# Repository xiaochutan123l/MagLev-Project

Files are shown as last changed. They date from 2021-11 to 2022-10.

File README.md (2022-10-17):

MagLev-Project

[中文版Chinese](https://github.com/xiaochutan123l/MagLev-Project/blob/main/docs/%E4%B8%8A%E6%8B%89%E5%BC%8F%E7%A3%81%E6%82%AC%E6%B5%AE.md)

Pull-up magnetic levitation based on Arduino board.

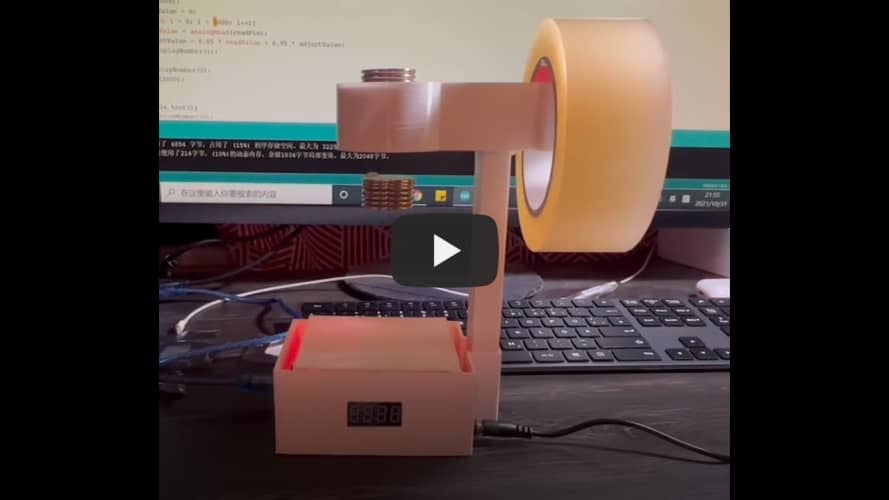
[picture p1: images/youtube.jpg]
(https://youtu.be/WY3Qidg5Ipc)

## Introduction

MagLev-Project is a magnetic levitation project like its name.  Magnet levitation with Arduino or some other MCU is actually an old stuff. There are many tutorial and demonstration on the internet. Here i will share my code and the experience of making it. It may help someone who also wants to make a magnetic levitation device. 

There two types of magnet levitation principle: `Pull-up` and `Push-down`. This project is the other type `Pull-up`. This project includes two versions, `basic version` (manual set parameters for each floater) and `weight adaptive` version.

## Principle

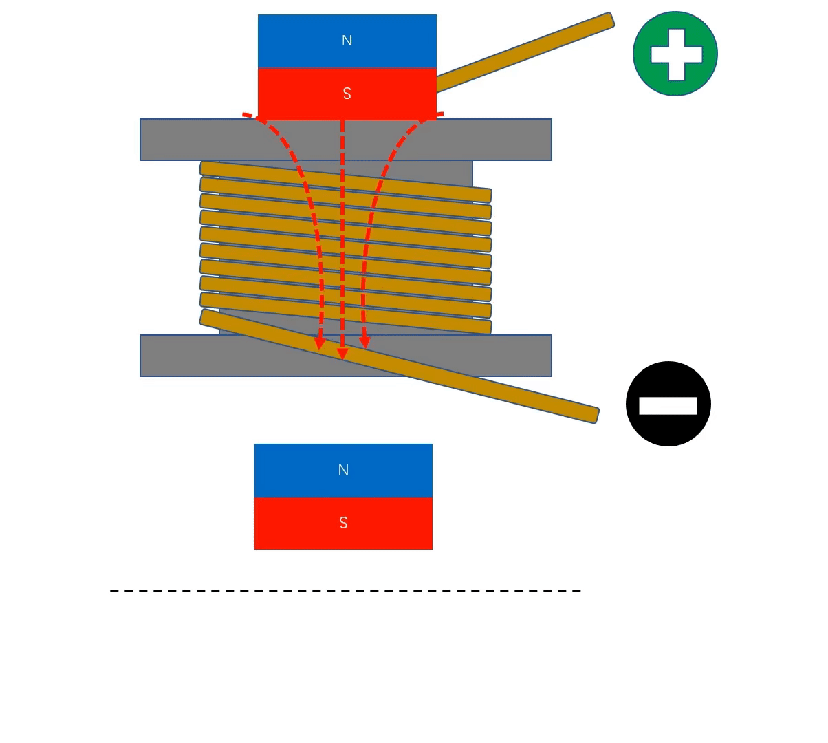
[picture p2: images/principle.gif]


The principle of the levitation is illustrated as in the Gif. The above magnet provides a pull force which can counteract the gravity of the bottom magnet(floater), this critical position is the `AdjustValue` which we want the floater to float. With the help of the above magnet, the electromagnet(copper coil) needs relatively small force to keep the floater at the critical position. 

We can see in this Gif, the levitation process is dynamic. If the floater goes down or up, we can control the coil to produce a pull or push force, by changing the electrodes. The Hall-effect sensor is very sensitive, thus a slight movement of the floater will be detected, and a corresponding controlling for the coil will then be taken. The floater can float stably at a fixed position.

## Hardware components

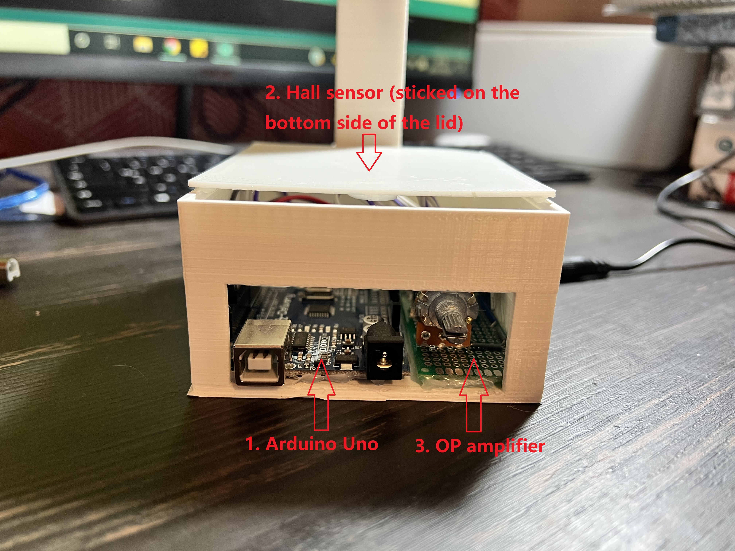
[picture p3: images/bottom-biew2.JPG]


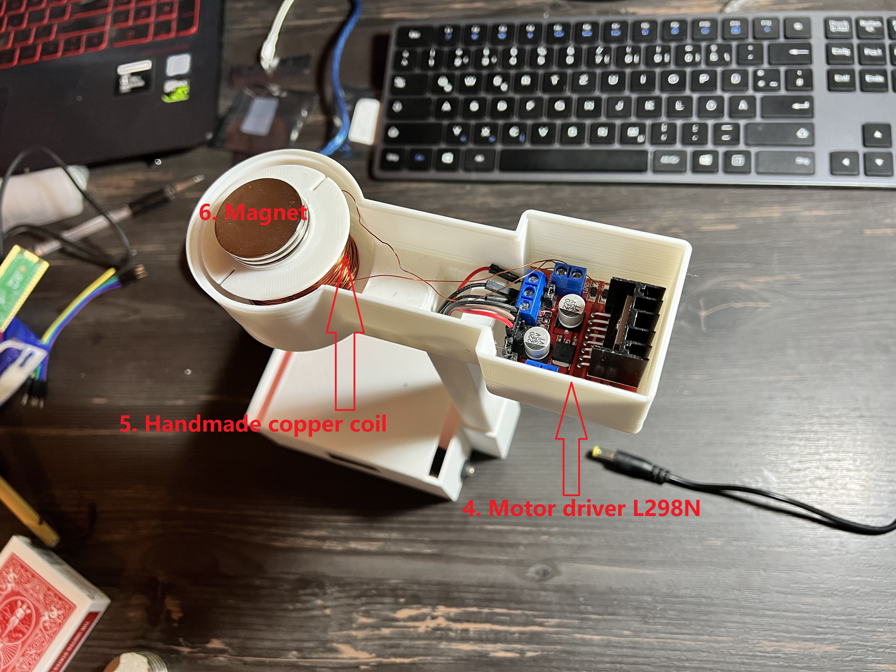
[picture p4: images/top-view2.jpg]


#### 1. Arduino Uno (it can be any MCU)

#### 2. Hall sensor

I use `49E011BD`, other Linear Hall effect sensors with similar Supply Voltage (3 - 6.5V) are also suitable.

Hall sensor can detect and transfer the magnetic field to voltage signal. It's used to detect the position of the floater.

#### 3. Operational amplifier

Since the Hall sensor can only output a very small range of voltage, a OP amplifier is used to amplify the voltage signal, as the input signal for Arduino Uno. (`LM358N` is used).

#### 4. Motor driver module

 `L298N` Motor driver module, it provides H-Bridge DC Motor Control, it's used to drive the copper coil as a electromagnet. Pull-up type requires only one copper coil, so only half of the H-Bridge is needed.

#### 5. Magnet

Two stack of magnets are used. One is the floater, another is the magnet on the copper coil, it can counteract the gravity of the floater, in this way only few energy needed for the levitation. 

### Schematic diagram

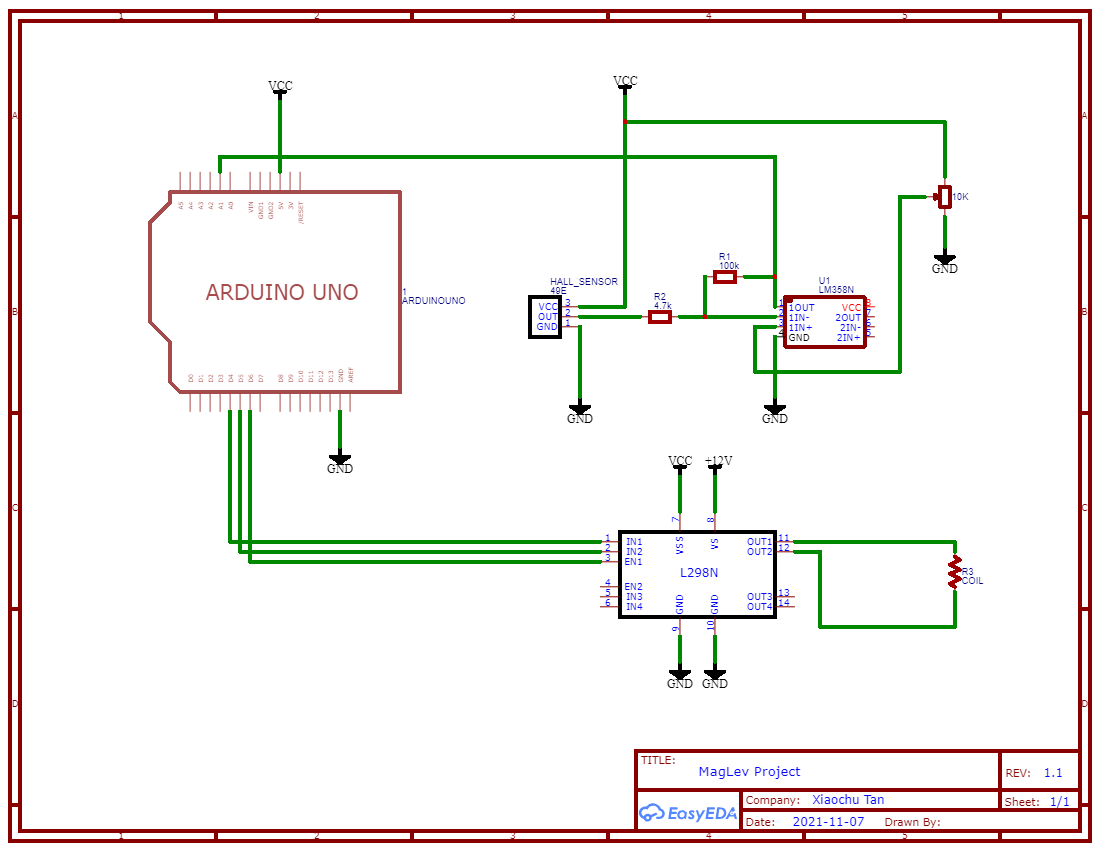
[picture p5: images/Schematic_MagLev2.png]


## Algorithm

The source code is not complicated, so here are just some tips and necessary explanation.

### 1. Basic version - PID

##### Find the `AdjustValue`: 

Just grab the floater below the coil, move the floater. You can feel in some position the floater is weightless, if you move up the floater a little bit, it will be caught by the above magnet. A position slight above this banlance point is the `AdjustValue`, at here coil only need to provide repulsive force, the gravity on floater will be compensated by the magnet above.

The value can be observed by *Serial Monitor* or a digit display like i used.

#### Tune the PID parameter:

Only `P` and `D` are used. Try different `P` first by size, then you can feel the repulsive force on the floater from coil if you move the floater near to the above magnet, keep increase the `P` size, once you see the floater waggles for one or twice becouse of the force from coil and the gravity, that means the `P` value is now a suitable value, the coil can privide enough force to compensate the attractive force from above magnet.

Then try different `D` value by size, but exponentially, 0.001-0.01, 0.01-0.1, 0.1-1 an so on. Until floater floats stable, this combination of `P` and `D` is the final parameter. 

Tip: try with increasing parameter with large step to roughly find a interval, then determine the prise one.  

#### Filter:

Due to the sensitivity of the Hall sensor and the impact from the environment, a filter is necessary. I used the mean value of multiple reading, it works well for me.

### 2. Advanced version - Floater detection and weight adaptive

In order to avoid the boring parameter determination process, in the advanced version, the floater detection function is introduced. (the PID parameter should be determined first)

#### Floater detection:

At the very beginning, the initial read value from sensor will be recorded. If the floater comes in, the magnet field will cause a huge change of the read value. The difference of the current read value to the initial value is used to determined if there is a floater comes in or out.

#### Weight adaptive:

The `AdjustValue` is not set at the initial phase any more. Each time after a floater came in, the `AdjustValue` will be set (again). Just grab the floater at the weightless point for a several seconds, the program will find the `AdjustValue`. 

## References

1. [Magnet Levitation with Arduino](https://create.arduino.cc/projecthub/jsirgado/magnet-levitation-with-arduino-eeeee4)
2. [盗梦陀螺](http://www.diy-robots.com/?page_id=685)
3. [改进磁悬浮装置](http://www.pengzhihui.xyz/2018/05/08/maglev/)

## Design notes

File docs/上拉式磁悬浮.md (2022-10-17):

## 基于Arduino的上拉式磁悬浮.

[b站视频演示](https://www.bilibili.com/video/BV1of4y1M7mH?share_source=copy_web)

## 介绍

基于Arduino或者其他MCU的磁悬浮项目其实是一个很古老的东西，网上已经有很多的教程和演示。这里分享我的代码以及磁悬浮装置制作中的一些经验，可能可以帮助到同样想制作一个磁悬浮装置的小伙伴。

有两种常见的磁悬浮种类:`上拉式`和`下推式`。在这个项目中是`上拉式`，并且有两个版本，一个是`基础版本`，需要手动为每一个浮子设置参数，另一个是`重量自适应版本`，参数可以自动设置。

## 基本原理



上面的Gif图展示了上拉式磁悬浮的基本原理。上面的磁铁提供吸引力来抵消浮子的重力，这样一来我们就可以以浮子刚好被抵消重力的位置作为参数`AdjustValue`。而电磁线圈只需要提供相对比较小的力就可以让浮子保持在平衡位置。

浮子悬浮的过程是动态的，浮子往上跑就控制线圈给浮子排斥力，相反就给吸引力。霍尔传感器非常敏感，浮子微小的位置变化都可以被探测出来，从而通过控制算法可以使浮子相对稳定的悬浮在空中。

## 硬件部分





#### 1. Arduino Uno (也可以是其他MCU)

#### 2. 霍尔传感器

我使用的是`49E011BD`，其他的线性霍尔传感器其实都差不多，只要工作电压大概在3 - 6.5V之间都可以。霍尔传感器可以探测附近磁场变化并且输出电压信号，非常适合用来探测浮子的位置变化。

#### 3. 运算放大器

虽然霍尔传感器很敏感，但是输出的电压范围很小，说一需要加上运算放大器将输出电压进行放大，作为Arduino的输入信号。这里我使用的是`LM358N`。

#### 4. 电机驱动模块

`L298N`，它可以进行全桥DC电机控制，在这里被用来驱动线圈。

#### 5. 磁铁

浮子本身是磁铁，线圈上方的也是磁铁，我使用的都是铷磁铁。

### 电路原理图



## 算法部分

源码比较简单，这里就只说一下重要的几个点。

### 1. 基本版本-PID

#### 确定`AdjustValue`: 

装置制作好之后，拿着浮子放到线圈下方，不断调整位置，直到有个位置浮子重力即将被抵消，这个位置就作为平衡点位置`AdjustValue`，位于真正的平衡点稍微上一点点。这样一来，只需要驱动线圈给浮子斥力，浮子重力完全由上方的磁铁抵消。

可以通过Arduino IDE自带的串口监视器或者绘图器来确定具体值，我是用的4位数字显示器。

#### PID参数整定:

我只是用了P和D。先调P值，从小到大开始试，当P很小的时候，手持浮子向线圈慢慢靠近并不会感受到线圈对浮子的斥力，增大P值慢慢会感觉到线圈对浮子的力，继续增加P值，直到P达到一个临界值，刚好让浮子在线圈对作用力之下能上下晃动一两下，不会持续很多次，能在手不施力的情况下因为线圈和重力能上下晃动一两下就够了，证明此时的P值能够使线圈提供足够的斥力，让浮子不被上面的磁铁吸上去。（也可以把P稍微再调大一点，影响不大，不需要大到浮子剧烈震荡）

在P值确定后，用同样的方式从小到大寻找D值，建议指数增长，而不是线性增长，比如先在0.001到0.1之间试两三个数，然后0.1到1之间试几个数，然后1-10以此类推。随着D的增大能逐渐感觉到浮子可以越来越稳定地悬浮起来。当再增大D反而导致更不稳定的时候，就说明之前的D已经是最合适的值了。

如果怎么增大P或者D都不见好转，可以考虑乘以-1，来避免代码中方向弄反。

#### 滤波：

由于霍尔传感器很敏感，加上周围环境造成的波动，想要读取到一个稳定的值需要进行滤波处理。这里我使用的就是取平均值的方式，简单粗暴。
PS：可以加上一个电容进行硬件滤波，根据硬件滤波效果决定要不要再辅以软件滤波。

### 2. 改良版本 - 浮子检测和重量自适应

为了避免麻烦的位每个浮子设置平衡点的操作，我进行了改良。当然PID还是需要提前整定好的。

#### 浮子检测:

在装置刚运行的时候，也就是还没有把浮子放过去的时候，记录下当前的传感器值作为初始值。当浮子进来后，磁场变化会导致传感器读取值发生很大变化，浮子拿走后，读取值又会变回到初始值差不多大小（可能会有一定误差）。也就是说通过当前的传感器的值和初始值的差的大小，可以判断线圈下，传感器上有没有浮子。

#### 重量自适应:

浮子检测机制的引入，让我们可以对每个新进来的浮子进行一次平衡点位置的读取。一旦一个浮子进入范围，也就是我们用手拿着浮子放到线圈下方，需要在平衡位置保持几秒钟，在这几秒钟里，程序会持续读取传感器的值，以此获取浮子平衡位置的`AdjustValue`。一旦检测到悬浮中的浮子被拿走，就进入一个等待循环，直到下一次有浮子进入，重新开始读取平衡位置，然后进行悬浮的主循环。

## 参考

1. [Magnet Levitation with Arduino](https://create.arduino.cc/projecthub/jsirgado/magnet-levitation-with-arduino-eeeee4)
2. [盗梦陀螺](http://www.diy-robots.com/?page_id=685)
3. [改进磁悬浮装置](http://www.pengzhihui.xyz/2018/05/08/maglev/)

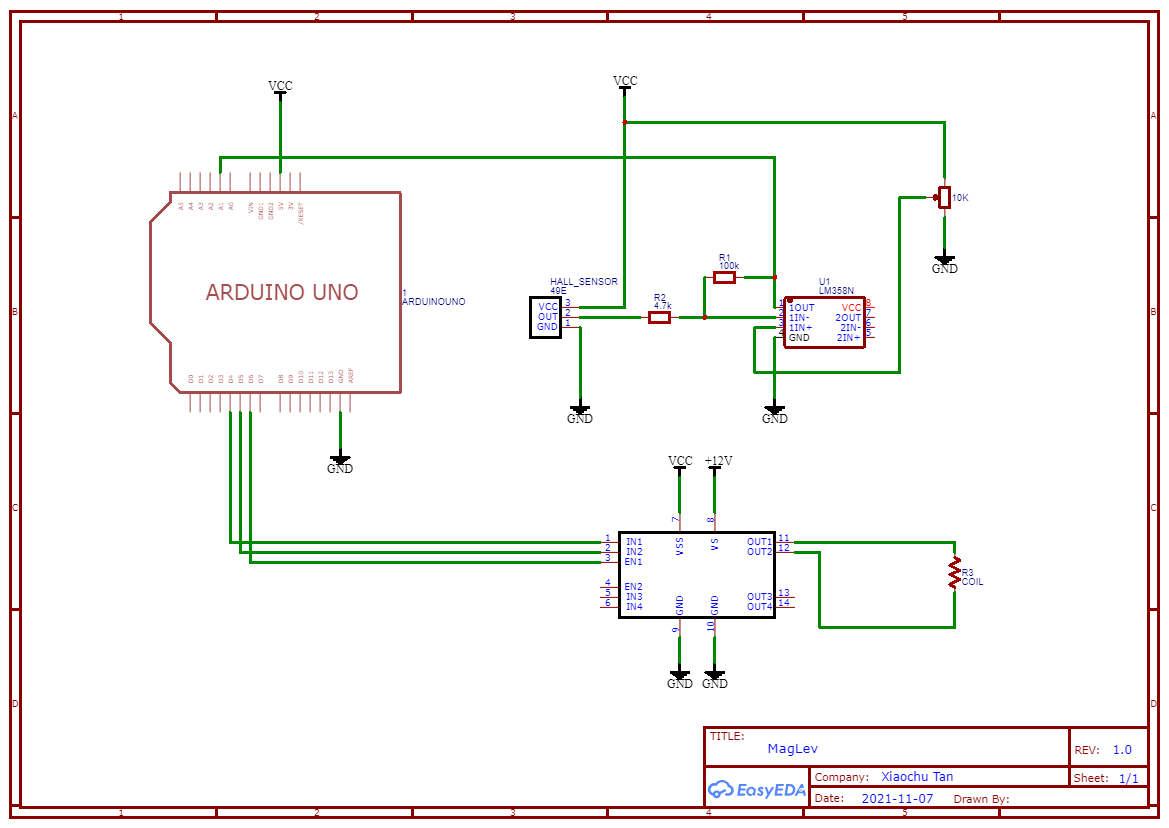
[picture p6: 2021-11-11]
images/Schematic_MagLev_2021-11-08-2.png

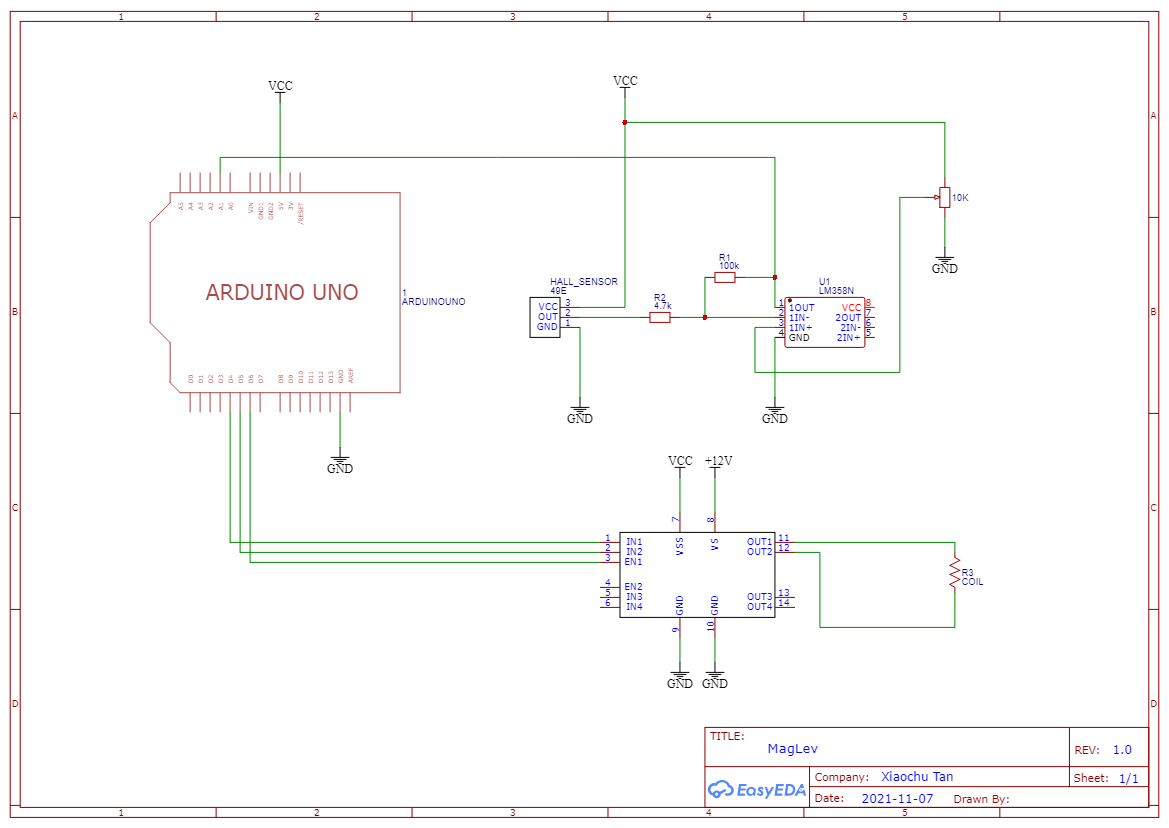
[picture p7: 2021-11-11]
images/Schematic_MagLev_2021-11-08.png

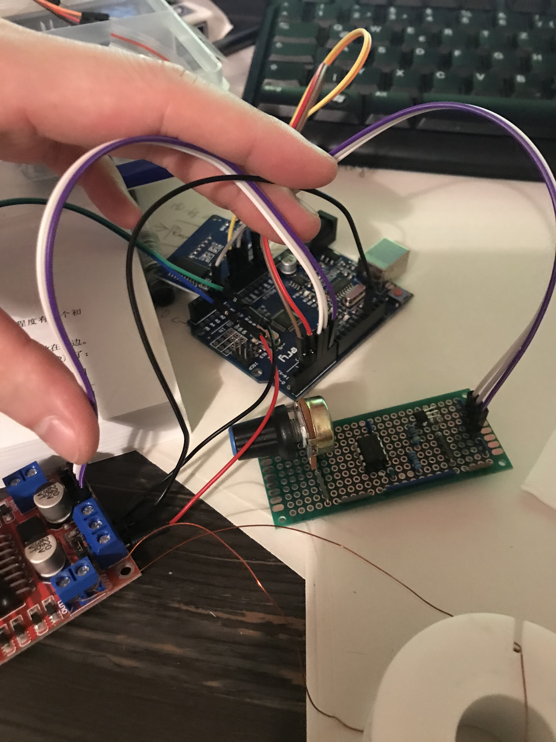
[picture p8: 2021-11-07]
images/circuit1.JPG

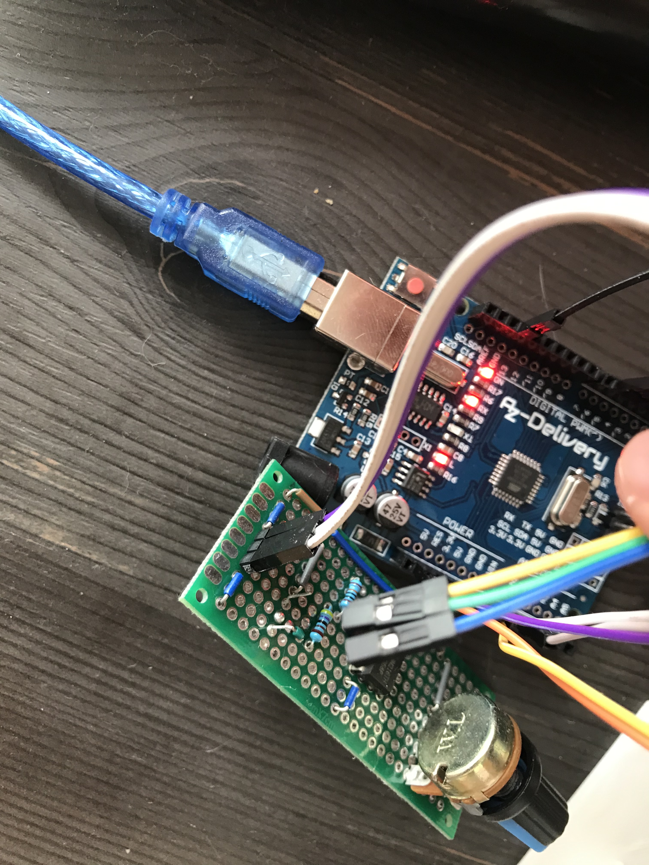
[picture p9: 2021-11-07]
images/circuit2.JPG

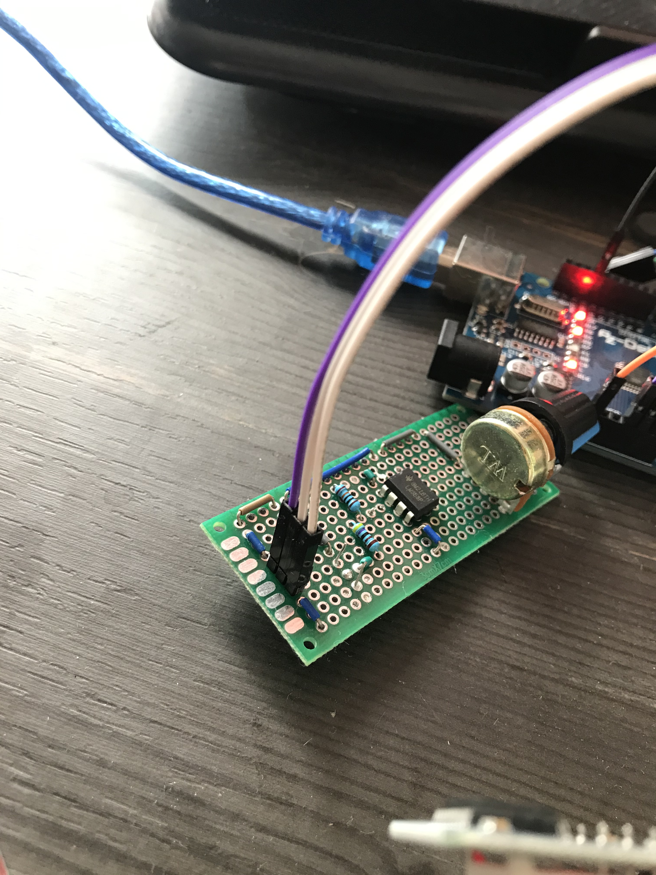
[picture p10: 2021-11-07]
images/hall-circuit.JPG

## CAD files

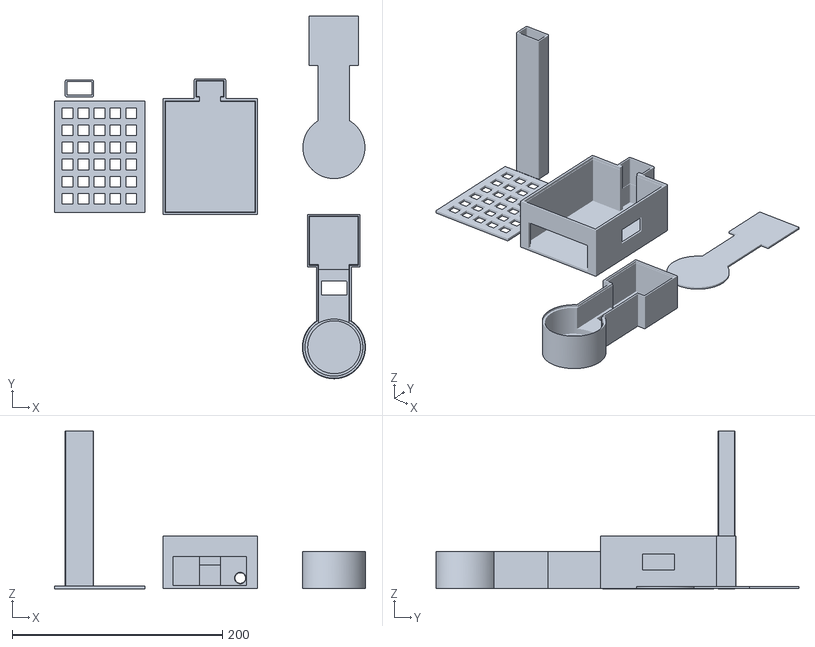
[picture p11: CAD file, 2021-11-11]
3d_model/full.stl
295.7 x 344.7 x 150.0

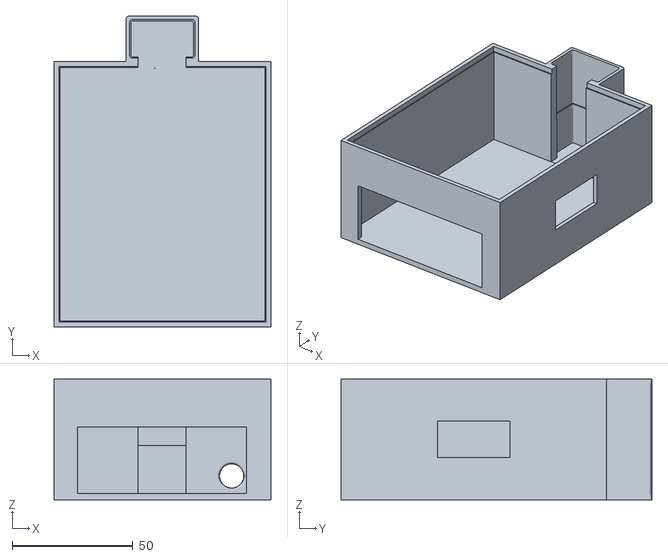
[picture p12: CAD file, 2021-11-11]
3d_model/base.stl
90.0 x 128.8 x 50.0

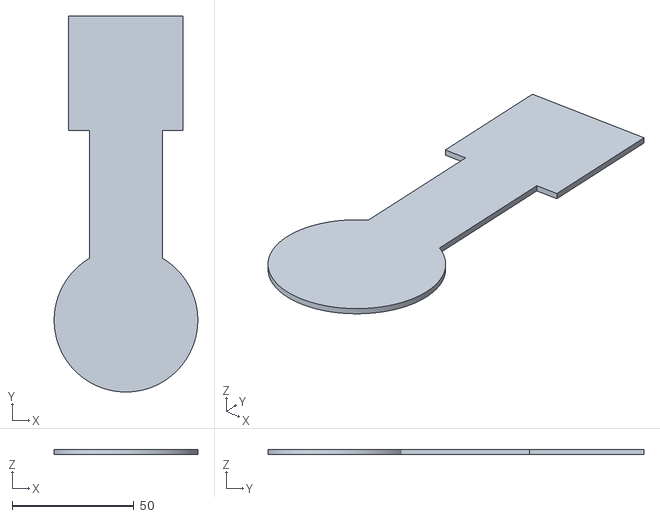
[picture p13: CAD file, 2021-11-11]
3d_model/top_lid.stl
59.0 x 154.4 x 2.01

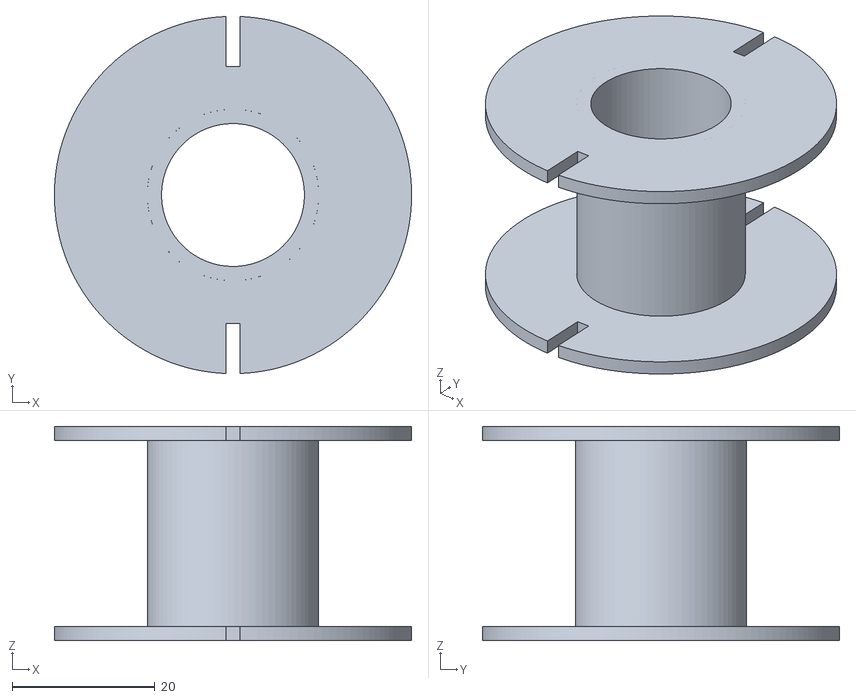
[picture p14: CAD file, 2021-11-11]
3d_model/coil-former.stl
50.0 x 50.0 x 30.0

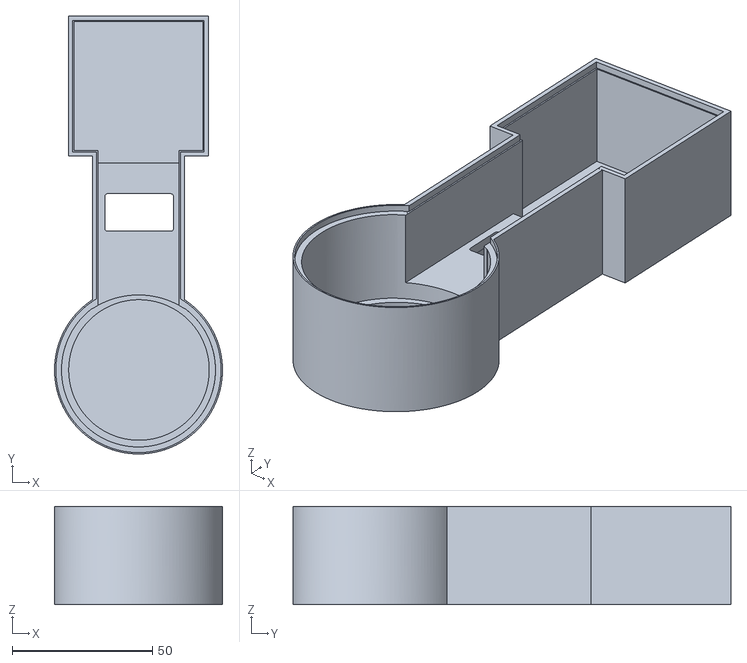
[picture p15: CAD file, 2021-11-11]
3d_model/top.stl
60.0 x 156.4 x 35.0

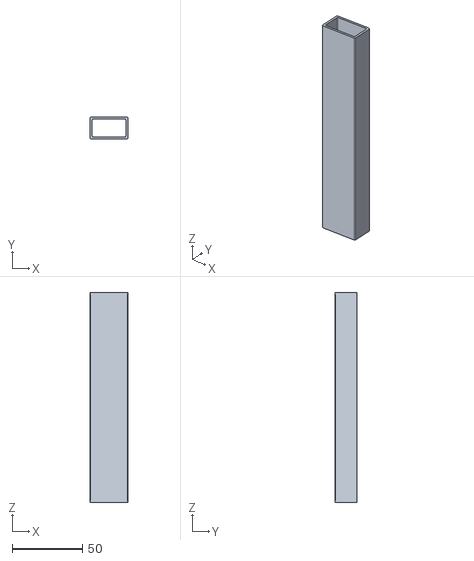
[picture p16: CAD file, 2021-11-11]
3d_model/pole.stl
27.0 x 16.0 x 150.0

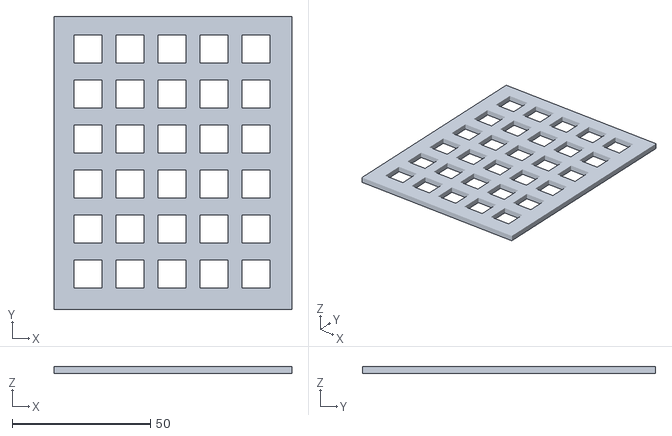
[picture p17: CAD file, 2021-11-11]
3d_model/base_lid.stl
86.0 x 106.0 x 2.50

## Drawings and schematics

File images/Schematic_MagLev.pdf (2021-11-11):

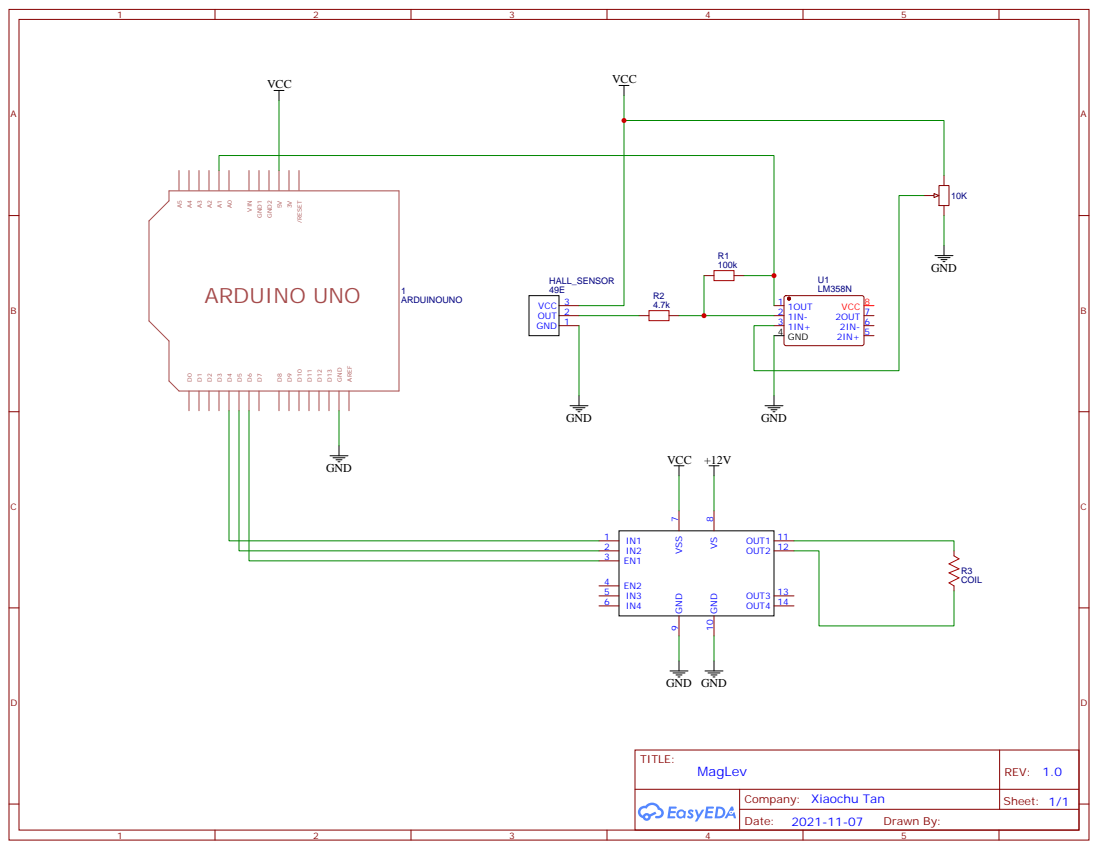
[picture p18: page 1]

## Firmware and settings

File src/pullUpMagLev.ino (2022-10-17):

/*
The basic version of the pull-up magnet levitation. 
*/

#include <TM1637.h>

// Hall component.
const int readPin = A1;
int adjustPin = A2;
int readValue = 0.0;            
float adjustValue  = 240;         
float filtValue = 0.0;

// LedDisplay component.
int CLK = 2;
int DIO = 3;
TM1637 tm(CLK,DIO);

// L298N component.
int IN1Pin = 4;
int IN2Pin = 5;
int EA1Pin = 6;
bool flag = true;

// PID components.
float error = 0.0;
float prevError = 0.0;
float power = 0.0;
float kp = 20.0;
float kd = 5.0;
float derivative = 0.0;
float dt = 0.1;
float output = 0.0;

void setup() { 
  pinMode(readPin, INPUT);
  pinMode(adjustPin, INPUT);    
  pinMode(IN1Pin, OUTPUT);
  pinMode(IN1Pin, OUTPUT);
  digitalWrite(IN1Pin, flag);  
  digitalWrite(IN2Pin, !flag);
  digitalWrite(EA1Pin,HIGH);  

  // Set digit dispaly for debug and parameters adjusting.
  tm.init();
  //set brightness; 0-7
  tm.set(2);
}

void loop() {
  readValue = 0;
  for (int i = 0; i < 20; i++){
    readValue += analogRead(readPin);
    }
  filtValue = readValue / 20;
  error = filtValue - adjustValue;

  derivative = (error - prevError) / dt;
  power = (-kp * error) + (-kd * derivative);
  prevError = error;

  if (power > 255){
    power = 255;
    }
  else if (power < -255){
    power = -255;
    }
  // only provides push force to floater.
  if (power <= 0){
    flag = false;
    digitalWrite(IN1Pin, flag);  
    digitalWrite(IN2Pin, !flag);
    analogWrite(EA1Pin, -power);
  }
} 

void displayNumber(int num){   
  tm.display(3, num % 10);   
  tm.display(2, num / 10 % 10);   
  tm.display(1, num / 100 % 10);   
  tm.display(0, num / 1000 % 10);
}

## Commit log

2021-11-11 update 3d model files
    [base.stl, base_lid.stl, coil-former.stl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]
2021-11-11 update schematic diagram
2021-11-20 update both README and new schematic diagram
2022-10-17 修正中文版pid参数整定方法描述
2022-10-17 update PID adjustion part of readme
